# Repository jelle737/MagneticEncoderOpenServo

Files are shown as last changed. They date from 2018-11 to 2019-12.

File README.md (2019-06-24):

# MagneticEncoderOpenServo
A programmable servo capable of turning a defined 1 turn 360° (or more)

Video on youtube:

1 turn 360° servo (http://www.youtube.com/watch?v=oHWwntjVp9A "1 turn 360° servo")

* A programmable servo, based on ATMEGA328P, TLE5012B, MC34931 or DRV8837, using the arduino enviroment
* It's a defined travel servo, capable of going beyond the limits that a potentiometer has, without adding extra gears. It uses a magnet encoder to read it's position instead of a potentiometer.

More information and images are to be found [on this rc groups thread](https://www.rcgroups.com/forums/showthread.php?3154439-1-turn-360%C2%B0-servo "1 turn 360° servo").

## Software

The software programmed as is has a travel of 376° between the control pulses of 1000µs and 2000µs. The pulses can be wider but *as is* it is limited between around 800µs and 2200µs. providing a travel of more then 450°.

The software can be reprogrammed to do the following:
* Become a continious rotating servo.
* Be a multiple turn servo, like a 10 turn sail winch servo.
* Be current limited, the hardware is capable but not software implemented.
* Have a speed limited movement.
* Be a digital classic servo with a travel of just 90° or 180°.
* Be programmed as time lapse very slow turning servo since there are 2^15 steps of precision.
* Be programmed to accept commands instead of a PWM signal, or have different interaction interfaces.

Dificulty of implementing varies on the topic.

Possible drawbacks:
* Since it uses a magnet, it might be interfered with by an external magnet.
* If the shaft is turned >180° degrees while unpowered the servo will skip a turn, it should not be turned >90° when powered down to prevent for this unwanted behaviour.
* Since there is no endstop there is a software implementation to catch where in a turn it was depowered. This uses EEPROM which has a 100000 write cycle. In my software implementation every 1/8th of a circle the position is saved. This is done in a ring memory containing 256 bytes and requires the old value to be erased (written with 0) and the next position to be written with the new position value. This means technically after 1600000 turns the atmega chips EEPROM might stop working correctly. If you succeed in breaking the EEPROM there are software solutions to prolong the atmega328p's life.

Possible improvements:
* In a fast movement the servo has a tendency to overshoot it's target value. At this moment a P&D is implemented in the PID, but I feel like the I could help out to not overshoot the target and have a more gracefull reach to the target value.
* Code could be improved to integrated safety features like current limiting.
* Code could be cleaned up.

## Hardware

The required parts next the pcb's and it's components are:
* A donor servo for it's housing, gears, motor and shaft of the potentiometer.
* A Diametrically Magnetised round magnet, hard to find can possibly be substitued by a cube magnet.
* Basic components of the hardware pcb are: ATMEGA328P, TLE5012B, MC34931 or DRV8837

## Open Source

This fork is software that is **open source** and is available free of charge without warranty to all users.

The license is GPL3.

## Project/Fork History

Based on OpenServo: https://github.com/ginge/OpenServo

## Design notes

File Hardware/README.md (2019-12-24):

# MagneticEncoderOpenServo
A programmable servo capable of turning a defined 1 turn 360° (or more)

## Servo Board & Schematic

First version to fit in a regular sized servo like Tower Pro MG995.

## ServoV2 Board & Schematic

Second slimed down version to fit a micro sized servo like EMAX ES08MA.

## Open Source

This fork is software that is **open source** and is available free of charge without warranty to all users.

The license is GPL3.

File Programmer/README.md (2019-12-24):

# MagneticEncoderOpenServo
A programmable servo capable of turning a defined 1 turn 360° (or more)

## Programmer

Code to run on an arduino nano to allow Arduino IDE to program the servo microcontroller with special bootloader over it's servo plug using 1 signal wire.
Softserial 1-wire code is based on the optiboot sofserial code with lots of trail and tweaks, and requires some special settings to compile within the arduino IDE.
The programmer uses it's regular RX and TX lines to communicate over usb with the computer/avrdude. It relays this data to PB0 (pin 8) on the microcontroller to interact with the servo (or µcontroller with custom bootloader).

A little bit more on it's development struggles can be read here: https://forum.arduino.cc/index.php?topic=625311.0

## Compile and install programmer

It should compile within arduino IDE with minor settings change within the IDE to allow for compilation.
The code has to be burned straight on the programmer chip, overwriting the bootloader on that chip as to not trigger that bootloader when uploading code to the servo µcontroller.
That code could look something like:
```
avrdude -c USBasp -p m328p  -v -e -U lock:w:0x3F:m -U flash:w:programmer.hex -U lock:w:0x0F:m
```

## Open Source

This fork is software that is **open source** and is available free of charge without warranty to all users.

The license is GPL3.

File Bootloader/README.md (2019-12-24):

# MagneticEncoderOpenServo
A programmable servo capable of turning a defined 1 turn 360° (or more)

## Bootloader

Minimal changes to the original bootloader to provide the functionality of softserial programming over 1 wire.

Some notheworty changes:
* 'output' and 'input' pin_def changes to same pin PB0 (pin 8).
* Usage of softserial, was already implemented.
* Change pinstate between tristate and output.
* Switch the reset flag with input state, high state is likely program state (reset flag), low state is likely pwm input and goes directly to program (no reset flag).
* If input high (likely to progam device) boot delay is 4 second.

## Compile & install bootloader

The bootloader can be compiled with the following command line: 
```
make LED_START_FLASHES=0 SOFT_UART=1 atmega328
```
The 4 seconds boot delay in case of a high signal can be changed in the code.

Upload the bootloader hex using a usbasp device with the following command:
Erase chip, unlock bootloader section and set fuses for clock and bootloader size
```
avrdude -c USBasp -p m328p  -v -e -U lock:w:0x3F:m -U efuse:w:0xFD:m -U hfuse:w:0xDA:m -U lfuse:w:0xFF:m
```
Program chip and lock bootloader section:
```
avrdude -c USBasp -p m328p  -v -e -U flash:w:bootloader.hex -U lock:w:0x0F:m
```

## Open Source

This fork is software that is **open source** and is available free of charge without warranty to all users.

The license is GPL3.

## Project/Fork History

Based on optiboot bootloader (by WestfW): https://github.com/Optiboot/optiboot

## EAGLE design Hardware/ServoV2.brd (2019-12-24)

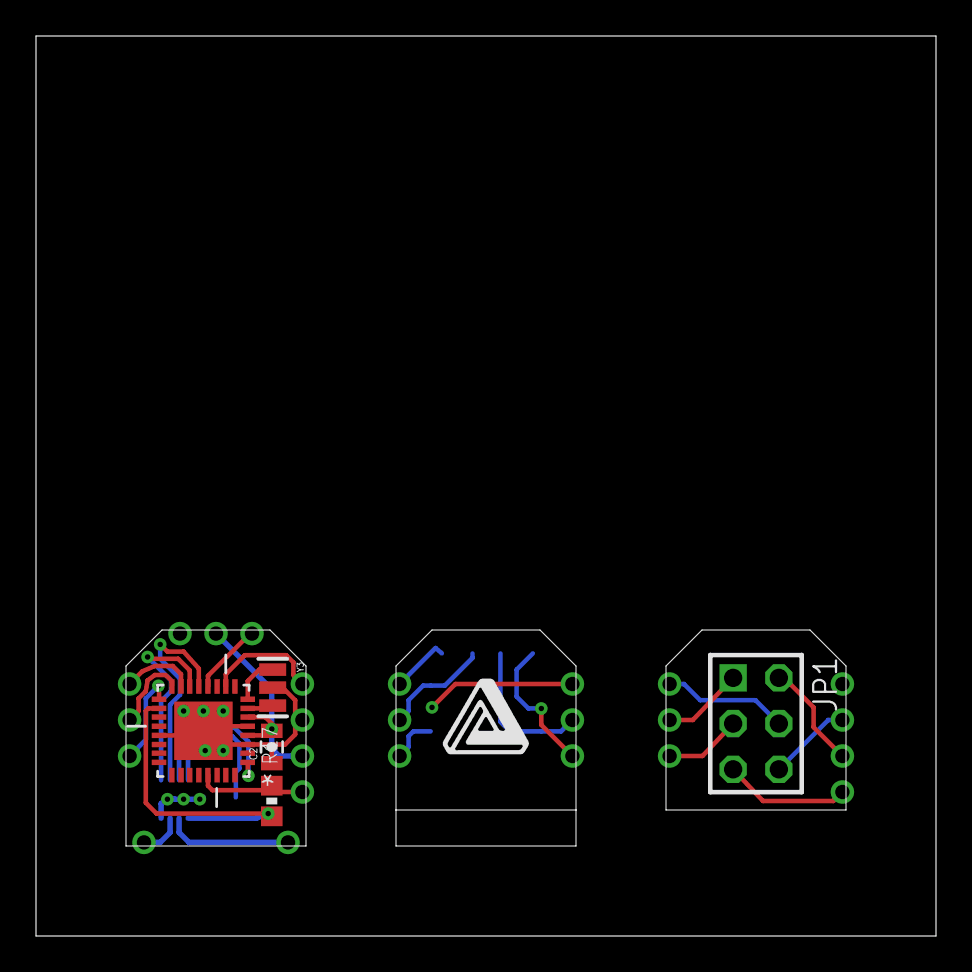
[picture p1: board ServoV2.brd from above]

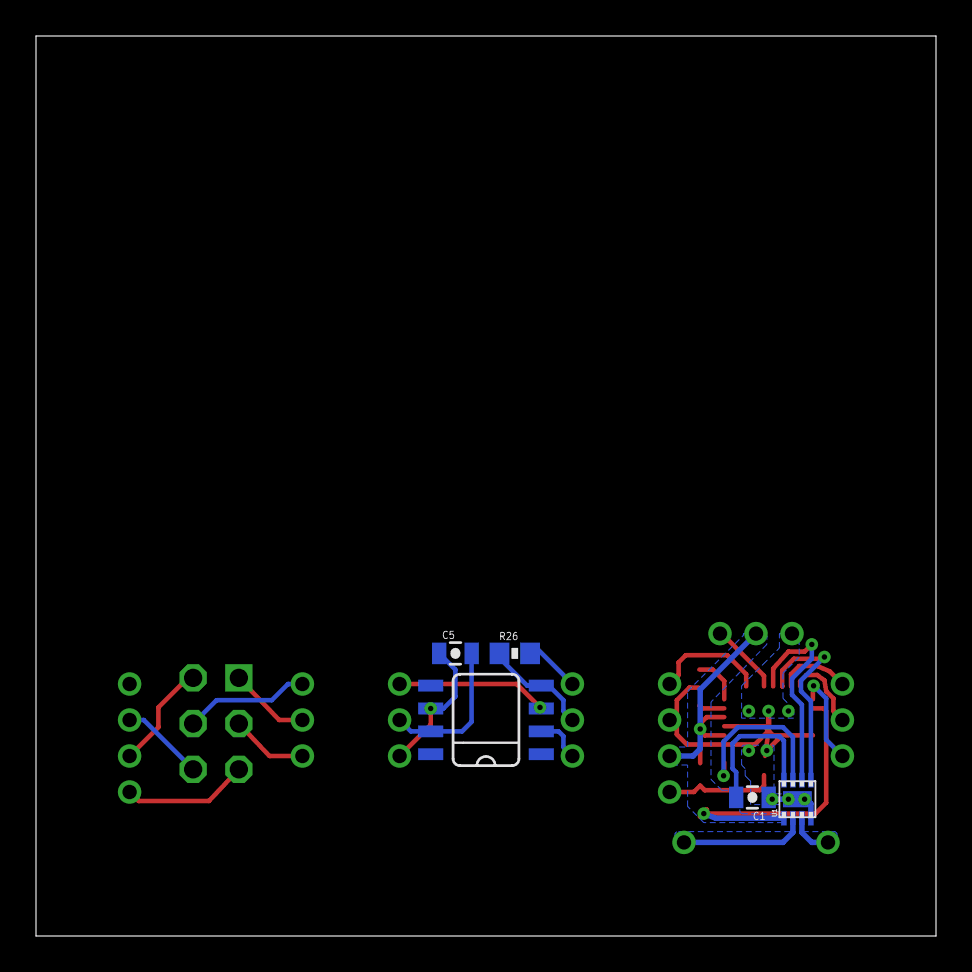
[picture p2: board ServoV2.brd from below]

Board: 2 copper layers, 50.0 x 50.0 mm, 13 parts (5 on the bottom side), 27 nets.

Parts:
C1, C2, C5: 100nF; 0805-CAP
IC4: TLE5012B E1000X; SO08
JP1: 2X03
R17: 1k; 0603
R26: 4.7k; 0603
U1: DRV8837; DSG
U2: ATMEGA328P-MU; QFN50P500X500X100-33N
U$1: 2TOPSIG
U$2: 2BOTSIG; 2BOTTOMSIG
U$3: PRGRMR
Y3: 16MHz; RESONATOR

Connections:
D3~: U1.7, U2.1
D6~: U2.10, U$2.P$7
D8: U2.12, U$2.P$3
D9~: U1.6, U2.13
D10/SS: U1.5, U2.14
D11~/MOSI: U2.15, U$2.P$4
D12/MISO: U2.16, U$2.P$5
D13/SCK: U2.17, U$2.P$6
GND: C1.1, C2.1, U1.4, U1.PAD, U2.3, U2.5, U2.21, U2.33, U$2.P$1, U$2.P$8, Y3.2
MISO: IC4.4, R26.1, U$1.P$5
MOSI: R26.2, U$1.P$4
OUT1: U1.2, U$2.P$11
OUT2: U1.3, U$2.P$10
PGND: JP1.6, U$3.P$8
PMISO: JP1.1, U$3.P$5
PMOSI: JP1.4, U$3.P$4
PRST: JP1.5, U$3.P$1
PSCL: JP1.3, U$3.P$6
PVCC: JP1.2, U$3.P$9
RESET: R17.2, U2.29, U$2.P$12
SCK: IC4.2, U$1.P$6
SS: IC4.3, U$1.P$7
TGND: C5.2, IC4.7, U$1.P$8
TVCC: C5.1, IC4.6, U$1.P$9
VCC: C1.2, C2.2, R17.1, U1.1, U1.8, U2.4, U2.6, U2.18, U$2.P$2, U$2.P$9
XTAL1: U2.7, Y3.3
XTAL2: U2.8, Y3.1

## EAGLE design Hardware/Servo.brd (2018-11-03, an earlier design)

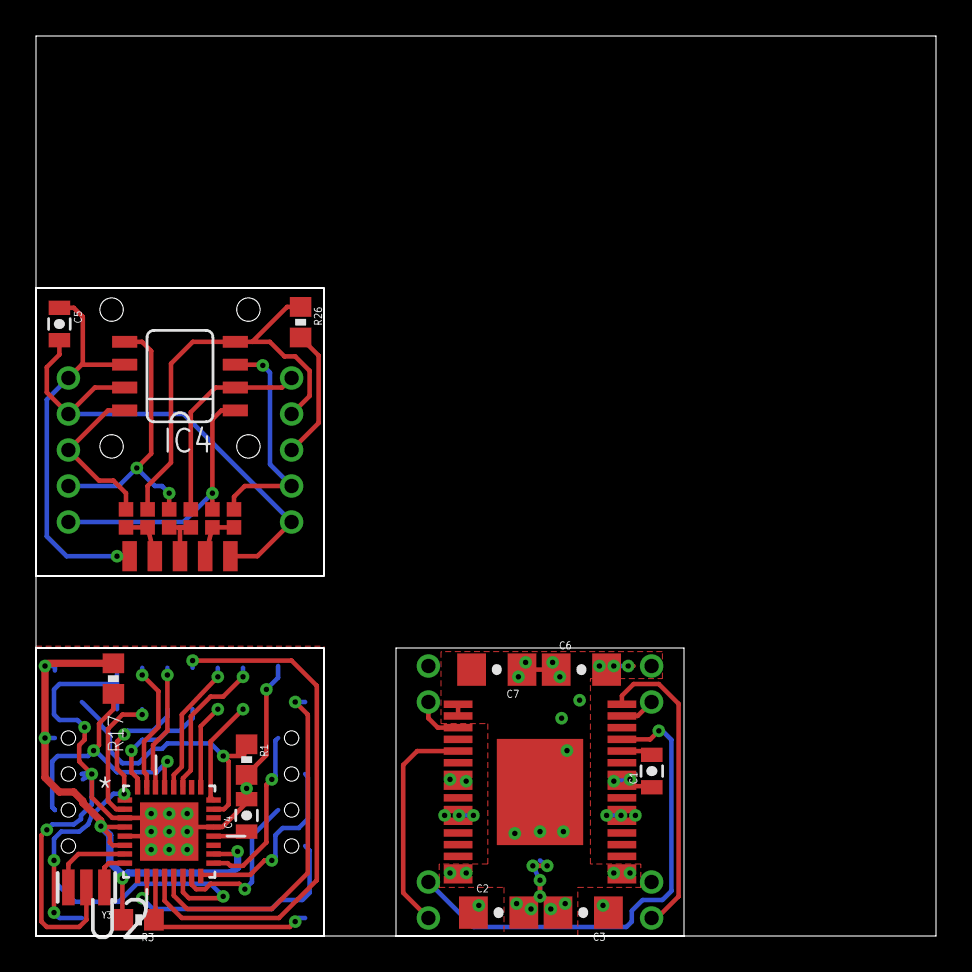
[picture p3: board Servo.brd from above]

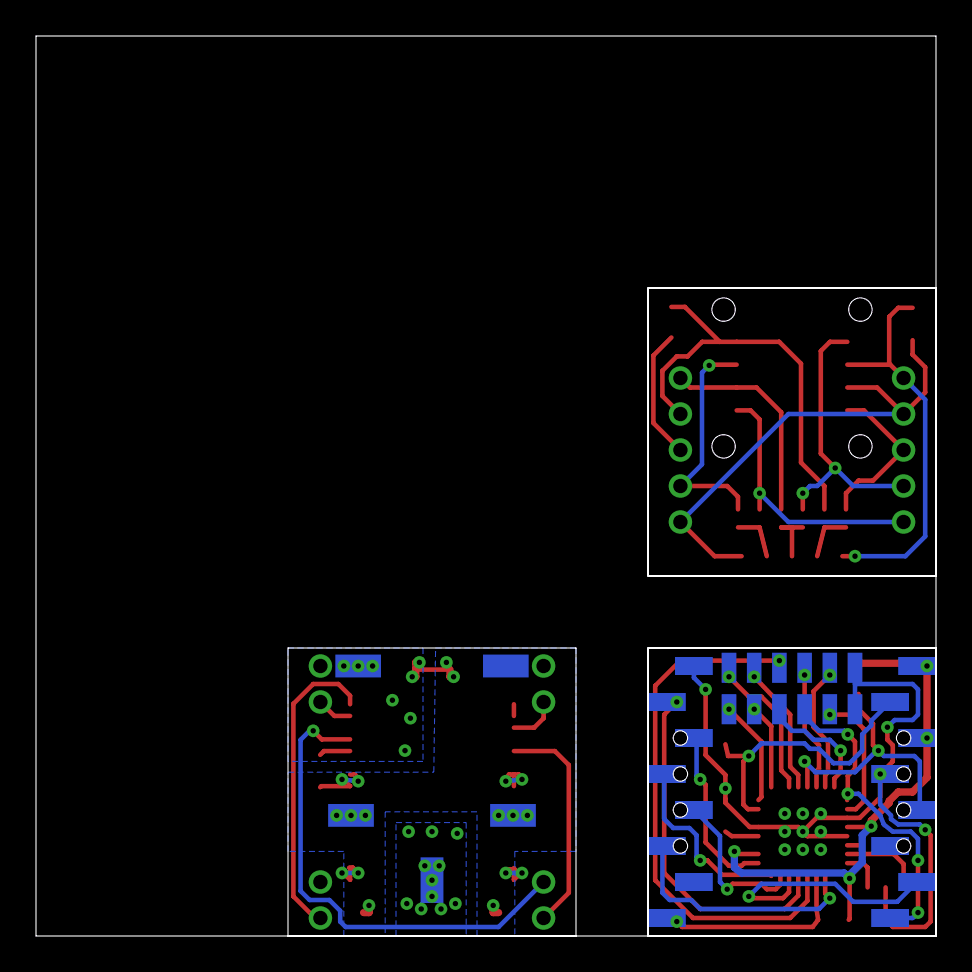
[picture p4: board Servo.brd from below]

Board: 2 copper layers, 50.0 x 50.0 mm, 25 parts (6 on the bottom side), 46 nets.

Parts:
C1: 30-100nF; 0805-CAP
C2, C3, C6, C7: 1.0uF; 1206-CAP
C4: 0.33uF; 0805-CAP
C5: 100nF; 0805-CAP
IC4: TLE5012B E1000X; SO08
R1: 430; 0603
R3: 2k; 0603
R17: 1k; 0603
R26: 4.7k; 0603
U2: ATMEGA328P-MU; QFN50P500X500X100-33N
U$1: MIDDLE; MIDDLE2
U$2: TOP
U$3: BOTTOM
U$4: MC34931EK
U$5, U$6, U$7, U$8, U$14: PAD
U$10: MIDDLE3
U$13: TOP2
Y3: 16MHz; RESONATOR

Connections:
A0: R1.1, U2.23, U$1.7
A1: U2.24, U$10.7
A2: U2.25, U$10.8
A4: U2.27, U$10.1
A5: U2.28, U$10.2
AREF: C4.1, U2.20
BGND: C2.2, C3.2, C6.2, C7.2, U$3.8, U$4.P$1, U$4.P$2, U$4.P$15, U$4.P$16, U$4.P$17, U$4.P$18, U$4.P$33, U$7.P$1, U$14.P$1
D0/RX: U2.30, U$10.4
D1/TX: U2.31, U$10.5
D2: U2.32, U$10.9
D3~: U2.1, U$1.1, U$10.10
D4: U2.2, U$10.11
D6~: U2.10, U$1.11
D7: R3.1, U2.11, U$1.9
D8: U2.12, U$10.3
D9~: U2.13, U$1.15
D10/SS: U2.14, U$1.2
D11~/MOSI: U2.15, U$1.12
D12/MISO: U2.16, U$1.13
D13/SCK: U2.17, U$1.14
EN: U$3.1, U$4.P$5
FAULT: U$3.5, U$4.P$32
FB: U$3.3, U$4.P$3
IFA: IC4.5, U$2.2, U$13.13
IFB: IC4.8, U$2.3, U$13.11
IFC: IC4.1, U$2.1, U$13.15
MGND: C4.2, R1.2, U2.3, U2.5, U2.21, U2.33, U$1.5, U$1.16, U$10.6, U$10.12, Y3.2
MISO: IC4.4, R26.1, U$2.9, U$13.12
MOSI: R26.2, U$2.8
MVCC: R3.2, R17.1, U2.4, U2.6, U2.18, U$1.6, U$1.8
unnamed: U$13.21, U$13.22, U$13.32
unnamed: U$13.23, U$13.24, U$13.33
unnamed: U$13.25, U$13.26, U$13.34
unnamed: C1.2, U$4.P$28
OUT1: U$4.P$10, U$4.P$11, U$6.P$1
OUT2: U$4.P$22, U$4.P$23, U$5.P$1
PWM1: U$3.7, U$4.P$31
PWM2: U$3.2, U$4.P$29
RESET: R17.2, U2.29, U$1.4
SCK: IC4.2, U$2.10, U$13.14
SS: IC4.3, U$2.7, U$13.16
TGND: C5.2, IC4.7, U$2.4, U$2.6, U$13.35
TVCC: C5.1, IC4.6, U$2.5, U$13.31
VIN: C1.1, C2.1, C3.1, C6.1, C7.1, U$3.4, U$4.P$7, U$4.P$8, U$4.P$25, U$4.P$26, U$8.P$1
XTAL1: U2.7, Y3.3
XTAL2: U2.8, Y3.1

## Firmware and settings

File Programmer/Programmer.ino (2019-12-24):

/* Ports for soft UART */
#define UART_PORT   PORTB
#define UART_PIN    PINB
#define UART_DDR    DDRB
#define UART_TX_BIT PB0
#define UART_RX_BIT PB0

#define STK_OK 0x10

#define BAUD_RATE 115200

#define SERIAL_TIMEOUT 15
#define SERIAL_TIMEOUT_LONG 200

uint8_t buf[300];
uint8_t ch;

void setup() {
  Serial.begin(115200);
  /* Set TX pin as output */
  UART_DDR |= _BV(UART_TX_BIT);
  /* Set TX pin as input = default (tri state pin?) */
  //UART_DDR &= ~_BV(UART_TX_BIT);
  /* SET_UART_PIN (line low) */
  //UART_PORT &= ~_BV(UART_TX_BIT);
  /* CLEAR_UART_PIN (set high) */
  UART_PORT |= _BV(UART_TX_BIT);
  /* READ_UART_PIN */
  //UART_PIN & _BV(UART_RX_BIT);
  /* Call uartdelay to have delayfuntion included in code */
  uartDelay();
}


void loop() {
  if (Serial.available()) {      // If anything comes in Serial (USB),
    int buflen = 0;
    buf[buflen++] = Serial.read();
    // Temporarily set timer2 to count ticks/128
    TCNT2 = 0;
    TCCR2B = (1<<CS22) | (1 << CS20);
    // Buffer data until the serial timeout
    while(TCNT2 < SERIAL_TIMEOUT){
      if(Serial.available()){
        buf[buflen++] = Serial.read();
        TCNT2 = 0;
      }
    }
    // Set timer2 back to normal
    TCCR2B &= 0b11111000;
    cli();
    putch(buf[0]);
    for(int i=1; i<buflen; i++){
      putch(buf[i]);
    }
    TCNT2 = 0;
    TCCR2B = (1<<CS22) | (1 << CS20);
    UART_DDR &= ~_BV(UART_TX_BIT);
    // Buffer data until the serial timeout
    while(TCNT2 < SERIAL_TIMEOUT){
      if(!(UART_PIN & _BV(UART_RX_BIT))){
        ch = getch();
        Serial.write(ch);
        TCNT2 = 0;
      }
    }
    /* during programming the STK_OK messages comes after a delay, catch this here but allow timeout if not coming */
    if(ch != STK_OK){
      TCCR2B = (1<<CS22) | (1<<CS21) | (1 << CS20);
      TCNT2 = 0;
      while(TCNT2 < SERIAL_TIMEOUT_LONG){
        if(!(UART_PIN & _BV(UART_RX_BIT))){
          ch = getch();
          Serial.write(ch);
          TCNT2 = 255; //immediate timeout
        }
      }     
    }
    // Set timer2 back to normal
    TCCR2B &= 0b11111000;
    UART_DDR |= _BV(UART_TX_BIT);
    sei();
  }
}

// AVR305 equation: #define UART_B_VALUE (((F_CPU/BAUD_RATE)-23)/6)
// Adding 3 to numerator simulates nearest rounding for more accurate baud rates
#define UART_B_VALUE (((F_CPU/BAUD_RATE)-20)/6)
#if UART_B_VALUE > 255
#error Baud rate too slow for soft UART
#endif

#if UART_B_VALUE < 6
// (this value is a "guess" at when loop/call overhead might become too
//  significant for the soft uart to work.  It tests OK with the popular
//  "ATtinycore" chips that need SOFT_UART, at the usual clock/baud combos.)
#error Baud rate too high for soft UART
#endif

int uartbval(void){
  return UART_B_VALUE;
}

void putch(char ch) {
  //Serial.write(ch);
  //watchdogReset();
  __asm__ __volatile__ (
    //"   rcall uartDelay\n"
    //"   rcall uartDelay\n"
    "   com %[ch]\n" // ones complement, carry set
    "   sec\n"
    "1: brcc 2f\n"
    "   cbi %[uartPort],%[uartBit]\n"
    "   rjmp 3f\n"
    "2: sbi %[uartPort],%[uartBit]\n"
    "   nop\n"
    "3: rcall uartDelay\n"
    "   rcall uartDelay\n"
    "   lsr %[ch]\n"
    "   dec %[bitcnt]\n"
    "   brne 1b\n"
    :
    :
      [bitcnt] "d" (10),
      [ch] "r" (ch),
      [uartPort] "I" (_SFR_IO_ADDR(UART_PORT)),
      [uartBit] "I" (UART_TX_BIT)
    :
      "r25"
  );
}

uint8_t getch(void) {
  uint8_t ch;
  //#ifdef LED_DATA_FLASH
  //  LED_PORT ^= _BV(LED);
  //#endif
  //watchdogReset();
  __asm__ __volatile__ (
    "   rcall uartDelay\n"          // Get to middle of start bit
    "2: rcall uartDelay\n"              // Wait 1 bit period
    "   rcall uartDelay\n"              // Wait 1 bit period
    "   clc\n"
    "   sbic  %[uartPin],%[uartBit]\n"
    "   sec\n"
    "   dec   %[bitCnt]\n"
    "   breq  3f\n"
    "   ror   %[ch]\n"
    "   rjmp  2b\n"
    "3:\n"
    :
      [ch] "=r" (ch)
    :
      [bitCnt] "d" (9),
      [uartPin] "I" (_SFR_IO_ADDR(UART_PIN)),
      [uartBit] "I" (UART_RX_BIT)
    :
      "r25"
  );
  //#ifdef LED_DATA_FLASH
  //  LED_PORT ^= _BV(LED);
  //#endif
  return ch;
}

void uartDelay(){
  __asm__ __volatile__ (
    //"   rcall uartDelay\n"          // Get to middle of start bit
    "   rjmp  2f\n"
    "uartDelay: ldi r25,%[count]\n"
    "1: dec r25\n"
    "   brne 1b\n"
    "   ret\n"
    "2:\n"
    :
    :
      [count] "M" (UART_B_VALUE)
    //:
    //  "r25"
  );
}

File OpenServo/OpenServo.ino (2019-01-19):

#include <inttypes.h>
#include <avr/interrupt.h>
#include <avr/io.h>

#include "pwm.h"
#include "pid.h"
#include "pulsectl.h"
#include "swspi.h"
#include "timer.h"
#include "enc.h"
#include "storage.h"

#define EEPROM_VERSION 1

int16_t pwm;
int16_t position;

void setup() {
    if(eeprom_read_byte(0) !=  EEPROM_VERSION){
        storage_registers_defaults();
        eeprom_write_byte(0, EEPROM_VERSION);
    }
    pwm_init();
    storage_init();
    swspi_init();
    enc_init();
    pulse_control_init(enc_get_position_value());
    pid_init(reg_seek_position);
    timer_init();
    sei();
    pwm_enable();
}

void loop() {
    pulse_control_update();
  
    // Get the new position value.
    position = (int16_t) enc_get_position_value(); //0.2048..4096.y for x.0°..360°.y
  
    // Call the PID algorithm module to get a new PWM value.
    pwm = pid_position_to_pwm(position);
  
    // Update the servo movement as indicated by the PWM value.
    // Sanity checks are performed against the position value.
    pwm_update(position, pwm);
  
    // Store position just in case of power loss
    storage_update(position);
}

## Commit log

2018-11-03 Initial release project upload.
    [Servo.brd, Servo.sch]
2019-01-19 Mayor update, full PID controller, timeout timer fixed, full code cleanup, local and global variables instead of variable table.
    [OpenServo.ino, pulsectl.cpp, pwm.cpp]
2019-06-24 Fix spi timing to represent minium timings as in the datasheet of TLE5012B
    [pulsectl.cpp, swspi.cpp]
2019-12-24 Custom bootloader to allow for programming over the servo wire. 1-wire bootloader.
2019-12-24 Code for the dedicated programmer to work with the custom bootloader to allow for upload code over the servo plug. 1-wire programmer.
2019-12-24 Schematic and board design for the micro servo design of this project. Merry Christmas.
    [ServoV2.brd, ServoV2.sch]

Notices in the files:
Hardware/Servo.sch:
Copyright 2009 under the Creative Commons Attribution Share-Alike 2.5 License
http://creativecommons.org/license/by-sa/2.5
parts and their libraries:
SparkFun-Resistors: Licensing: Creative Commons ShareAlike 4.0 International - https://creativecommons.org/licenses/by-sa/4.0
